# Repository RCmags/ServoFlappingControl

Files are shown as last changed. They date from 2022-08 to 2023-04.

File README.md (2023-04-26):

# Servo controller for an ornithopter :airplane: :bird:
This sketch controls the servos used to power an RC ornithopter (Flapping MAV). Each servo is connected to a wing and flapped independently. 

## How it works
The program is designed to receive 4 PWM inputs from an RC receiver operating in [MODE 2](https://www.rc-airplane-world.com/rc-transmitter-modes.html) and will output 4 PWM signals for off-the-shelf hobby servos. Two servos control the wings and two servos control a V-tail. 

The _aileron (1) and elevator (2)_ channels are used to modify the motion of the wings and to control the tail. The dihedral angle of the wings is altered in unison with the elevator, while the aileron rotates them in opposite directions. Simultaneously, the frequency of the wing-oscillation can be modulated, such that the wings move faster during the downstroke or during the uptroke. Depending on whether this is done symmetrically or assymetrically, one can obtain pitch or roll control. 

<p align="center">
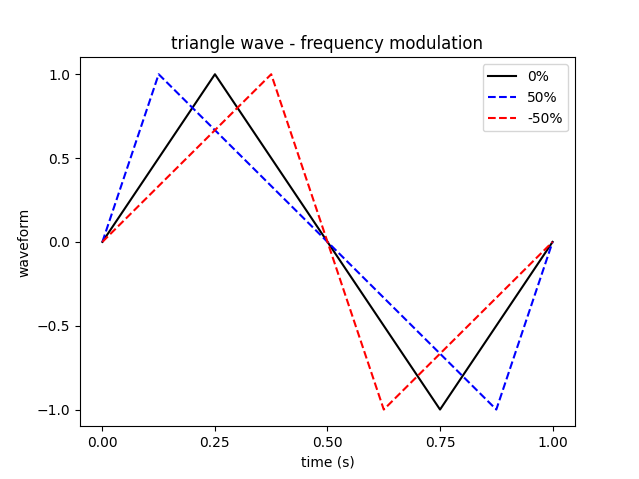
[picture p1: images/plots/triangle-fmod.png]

</p>

The _throttle channel (3)_ controls the amplitude of a fixed-frequency oscillation. By default, the waveform is a triangle-wave, but the throttle can also be used to truncate the wave so it looks more like a square wave. Using a square wave allows the servo to output more mechanical power, but the transition between strokes is very abrupt and stressful. The truncated-wave eases this transition while increasing power compared to a triangle wave.

<p align="center">
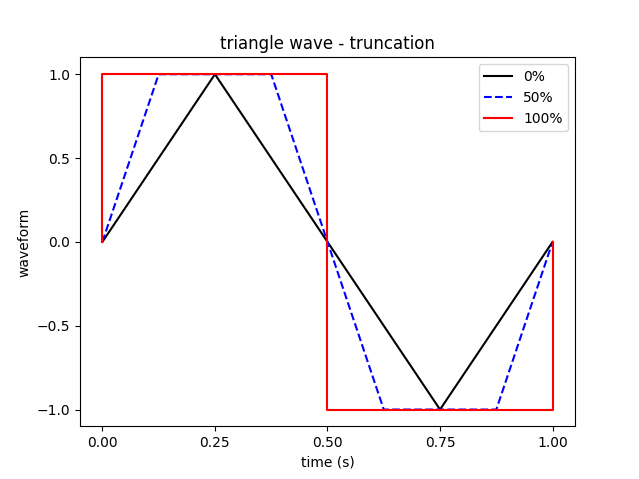
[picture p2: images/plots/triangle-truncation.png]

</p>

The _rudder channel (4)_ is used to assymetrically vary the amplitude of the wings. 

## Schematics
__Nano__: While the program was written for an Arduino Nano, it should be compatible with similar boards. If you don't use tail servos, simply remove them from the circuit and disable their code using the _parameters.h_ file.

<p align="center">
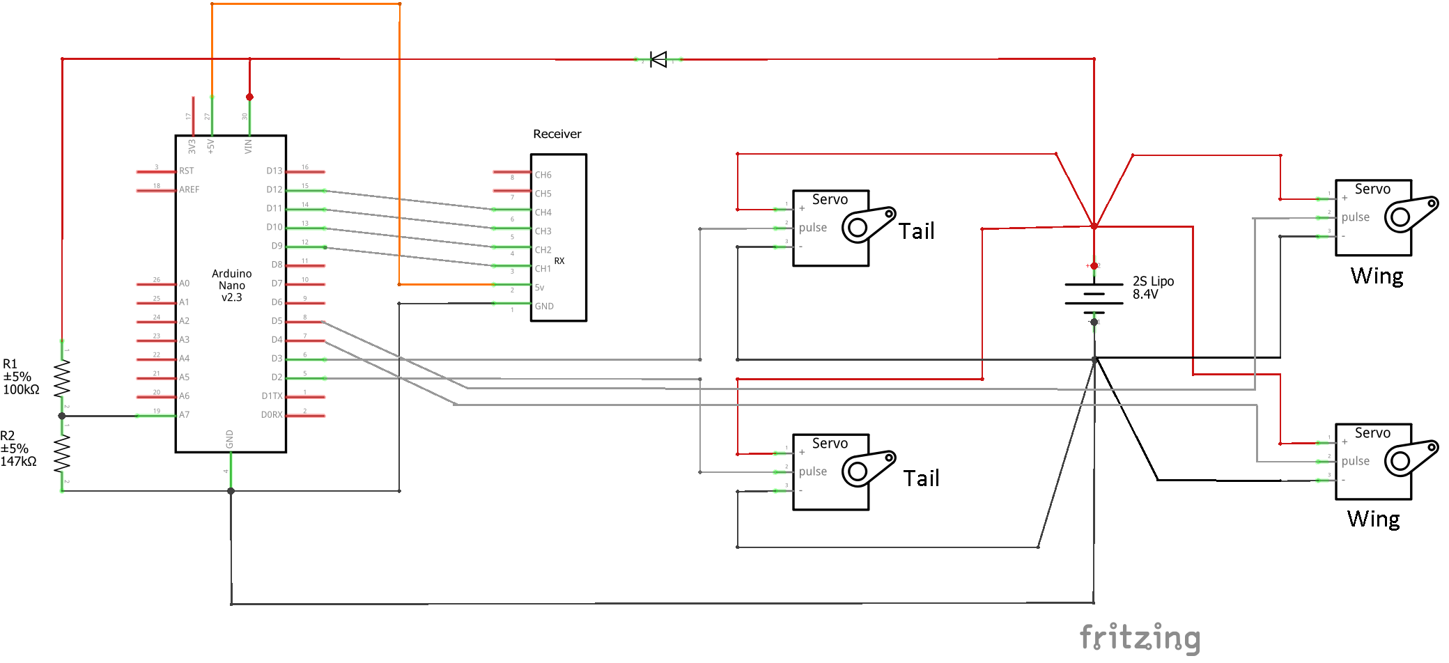
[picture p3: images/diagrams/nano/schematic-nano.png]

</p>

__DigiSpark ATTiny85__: As this microcontroller has fewer pins, it does not support tail servos or a rudder channel. Instead the assymetric amplitude can be mixed into the assymetric dihedral. 

<p align="center">
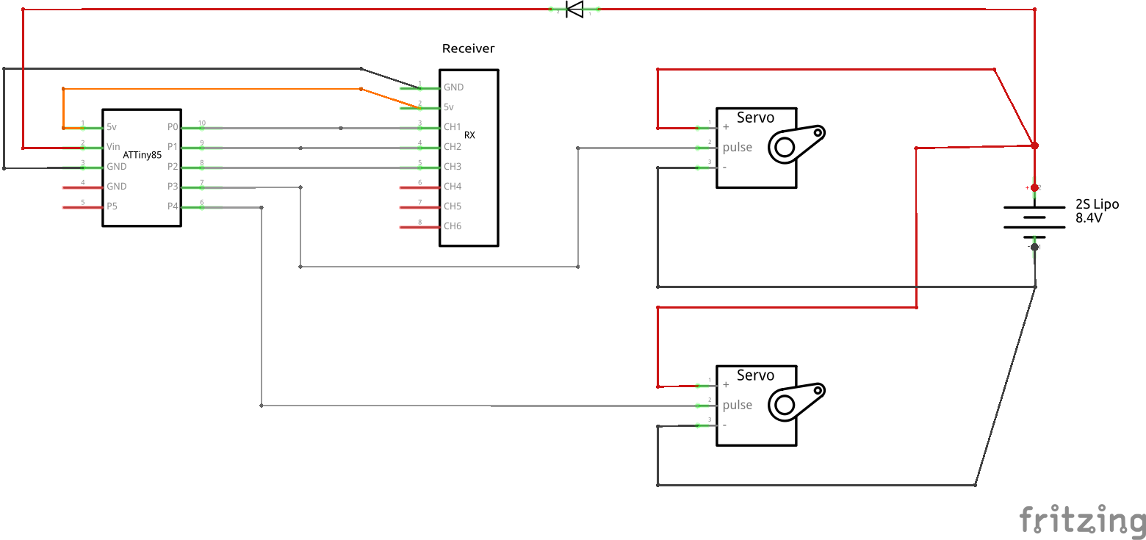
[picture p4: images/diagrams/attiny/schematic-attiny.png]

</p>

## Dependencies
The ATTiny code requires [ATTinyCore](https://github.com/SpenceKonde/ATTinyCore) to compile. 

## Example
See: [explanation and operation of the servo controller](https://youtu.be/T6NfZD_iuEs)

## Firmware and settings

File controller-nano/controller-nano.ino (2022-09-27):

/* ORNITHOPTER SERVO CONTROLLER */

/* Sketch for an arduino NANO that operates the servos of a radio controlled ornithopter. 
 * It commands two servos to flap the wings and (if desired) two servos to control a V-tail.
 * Author: RCmags https://github.com/RCmags
*/

//=============== Connections ================
// See included schematic
  // Inputs:
// Pin 9  -> Receiver CH1
// Pin 10 -> Receiver CH2
// Pin 11 -> Receiver CH3
// Pin 12 -> Receiver CH4
// Pin A7 -> Middle of voltage divider
  // Outputs:
// Pin 2  -> Left  wing servo
// Pin 3  -> Right wing servo 
// Pin 4  -> Left  tail servo 
// Pin 5  -> Right tail servo 

//=================== Code ===================
#include <Servo.h>
#include "parameters.cpp"

//---- global variables 
Servo servo[4]; 
volatile uint16_t pwm_input[4] = {0};

//----- Input signals
// PORTB = {8 .. 13} -> using pins {9 .. 12} = B00011110

/* port change interrupt to read PWM inputs from receiver */
ISR( PCINT0_vect ) {
  static uint32_t initial_time[4] = {0}; 
  static uint8_t port_last = PINB;  
  
  // port changes
  uint32_t current_time = micros(); 
  uint8_t port_rise = ~port_last & PINB;
  uint8_t port_fall = port_last & ~PINB;
  
  // find changing pins
  for( uint8_t index = 0; index < 4; index += 1) {
    uint8_t mask = B00000010 << index;  // Start at PCINT1   
    if( port_rise & mask ) {                
        initial_time[index] = current_time;
    } else if ( port_fall & mask ) {       
        pwm_input[index] = current_time - initial_time[index];
    }
  }
  port_last = PINB;    
}

void setupISR() {
  // enable PORTB interrupts  
  PCICR |= (1 << PCIE0);
  // enable PCINT for pins 9-12                                                   
  PCMSK0 |= (1 << PCINT1);                                              
  PCMSK0 |= (1 << PCINT2);                                              
  PCMSK0 |= (1 << PCINT3); 
  PCMSK0 |= (1 << PCINT4); 
  // set pins inputs
  pinMode(9,  INPUT_PULLUP);
  pinMode(10, INPUT_PULLUP);
  pinMode(11, INPUT_PULLUP);
  pinMode(12, INPUT_PULLUP);
}

//----- Input filter

/* convert PWM inputs to floats and center the readings */
void scaleInputs(float* output) {
  output[0] = float( int16_t( pwm_input[0] ) - PWM_MID );            // roll
  output[1] = float( int16_t( pwm_input[1] ) - PWM_MID );            // pitch
  output[2] = float( int16_t( pwm_input[2] ) - PWM_MIN )*GAIN_THRT;  // throttle
  output[3] = float( int16_t( pwm_input[3] ) - PWM_MID )*GAIN_YAW;   // yaw
}

float positive(float input) {
  return input < 0 ? 0 : input;  
}

//----- Servos

void setupServos() {
    #ifdef USE_TAIL_SERVOS
    pinMode(2, OUTPUT);
    pinMode(3, OUTPUT);
    servo[0].attach(2);
    servo[1].attach(3);
    #endif
    
    /* wing servos */
    pinMode(4, OUTPUT);
    pinMode(5, OUTPUT);
    servo[2].attach(4);
    servo[3].attach(5);
}

//---- Waveform

/* time variable between 0 and 1 */
float floorTime() {
  float t = micros() * 1e-6 * FREQ;
  return t - floor(t); 
}

/* trucanted triangle wave for times between 0 and 0.5 */
float halfWave(float x, float dm) {
  float m = 4 + dm;
  float im = 1.0/m;
  float x1 = 0.25 - im;
  float x2 = 0.25 + im;
  return x < x1 ? 1.0           :
         x < x2 ? -m*(x - 0.25) : -1.0;  
}

/* complete wave for times between 0 and 1 */
float fullWave(float x, float dm) {
  return x < 0.5 ? halfWave(x, dm) : -halfWave(x - 0.5, dm);
}

/* increase and decrease the slope of time */
float freqMod(float t, float ds) {
  constexpr float CONST = 1.0/float(PWM_MAX - PWM_MIN);  
  ds = ds * CONST;
  float m = 1.0/(1 + ds);        
  float im = 0.5/m;
  return t < im ? m*t : (0.5*t - 0.5)/(1 - im) + 1;
}

/* truncated triangle wave with variable ramp-up and ramp-down */
float fwave(float amp, float ds=0) {
  constexpr float CONST = GAIN_WAVE/(PWM_MAX - PWM_MIN); 
  float dm = positive(amp) * CONST;
  float t  = floorTime();
  float tm = freqMod(t, ds);
  return fullWave(tm, dm);
}

//----- Control mixes

/* v-tail mixing with adjustable pitch and roll gain */
void vmix(float* output, float* input, const float gain_x=1, const float gain_y=1) {
  float input_0 = input[0]*gain_x;
  float input_1 = input[1]*gain_y;
  float mix1 = input_1 - input_0;
  float mix2 = input_1 + input_0;
  // return output
  output[0] = mix1;
  output[1] = mix2;
} 

//----- Cutoff

/* low voltage cutoff based on voltage divider */
bool voltageCutoff() {
  constexpr float CONST = (5.0/1024.0)*(RESISTOR_1 + RESISTOR_2)/float(RESISTOR_1);
  static float mean = VOLT_MAX; 
  float volt = analogRead(A7) * CONST;
  mean += (volt - mean)*1e-4;              // average filter n=1e4
  return mean < VOLT_CUT ? HIGH : LOW;     // cutoff voltage
}

//----- Pitching moment correction

/* elevator trim that increases with throttle. Counters pitch-down moment caused by wing flapping */
float pitchTrim(float x) {
  constexpr float M = PITCH_TRIM_Y / float(PITCH_TRIM_X);
  return x < PITCH_TRIM_X ? M*x : PITCH_TRIM_Y;     
}

//----- Main loop

void setup() {
  setupISR();
  setupServos();
  pinMode(A7, INPUT);
}

void loop() {
  float input[4]; scaleInputs(input);

  #ifdef USE_TAIL_SERVOS
  float mix1[2]; vmix(mix1, input, GAIN_ROLL, GAIN_PITCH);
  
  float ptrim = pitchTrim( input[2] );   
  mix1[0] += ptrim;
  mix1[1] += ptrim;

  servo[0].writeMicroseconds( PWM_MID + mix1[0] + TRIM_TLEFT  );    // left tail
  servo[1].writeMicroseconds( PWM_MID - mix1[1] + TRIM_TRIGHT );    // right tail
  #endif
  
  /* wing servos */
  float mix2[2]; vmix(mix2, input, GAIN_ROLL_DH, GAIN_PITCH_DH);   // differential dihedral
  float mix3[2]; vmix(mix3, input,-GAIN_ROLL_FM, GAIN_PITCH_FM);   // frequency modulation
  
  bool cutoff = voltageCutoff();         // dissable flapping at low voltage 
  float amp1 = cutoff ? 0 : positive( input[2] + input[3] );
  float amp2 = cutoff ? 0 : positive( input[2] - input[3] );
  
  float wave1 = fwave( input[2], mix3[0] ); 
  float wave2 = fwave( input[2], mix3[1] ); 
    
  wave1 = wave1*amp1 + mix2[0];          // differential amplitude
  wave2 = wave2*amp2 + mix2[1];
  
  servo[2].writeMicroseconds( PWM_MID + wave1   + TRIM_LEFT   );    // left wing
  servo[3].writeMicroseconds( PWM_MID - wave2   + TRIM_RIGHT  );    // right wing
}

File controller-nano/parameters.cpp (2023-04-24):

/*      CONSTANT     |    VALUE   |  UNIT  |   DESCRIPTION */
/*=========================================================*/
// 1.  Flapping waveform
#define FREQ              3.1     // hz     // Wingbeat frequency [hz]. Use lowest frequency that achieves flight
#define GAIN_WAVE         6.0              /* Triangle wave to square wave gain (truncation). 
                                               A larger gain makes the waveform become more square-like with more throttle */
// 2. Control inputs [negate to reverse direction]
    // I. Base inputs:
#define GAIN_PITCH        1.0               // Tail elevator
#define GAIN_ROLL         1.0               // Tail aileron
#define GAIN_THRT         0.8               // Flapping amplitude. Increases with more throttle
#define GAIN_YAW          0.4               // Differential amplitude. Controlled by rudder
    // II. Differential dihedral:
#define GAIN_PITCH_DH     0.0               // Pitch: symmetric dihedral
#define GAIN_ROLL_DH      0.0               // Roll: asymmetric dihedral
    // III. Frequency modulation:
#define GAIN_PITCH_FM     0.0               // Pitch: wings fall at the same speed
#define GAIN_ROLL_FM      0.0               // Roll: One wing falls faster than the other

// 3. Servo trims 
#define TRIM_LEFT         -80     // us     // left  wing 
#define TRIM_RIGHT        50      // us     // right wing
#define TRIM_TLEFT        0       // us     // left  tail
#define TRIM_TRIGHT       50      // us     // right tail

// 4. Pitching moment correction 
#define PITCH_TRIM_X      250     // us     // Throttle PWM when trim reaches maximum value 
#define PITCH_TRIM_Y      -35  v0    // us     // Maximum pitch trim. Negate to reverse deflection

// 5. Low voltage cutoff [voltage divider]
#define RESISTOR_1        67000   // ohm    // Resistor from ground -> middle 
#define RESISTOR_2        118000  // ohm    // Resistor from middle -> voltage
#define VOLT_CUT          6.0     // volt   // cutoff voltage
#define VOLT_MAX          8.4     // volt   // fully charged voltage 

// 6. Output PWM signal [all servos]
#define PWM_MID           1500    // us     // Center/middle servo position
#define PWM_MIN           1100    // us     // Minimum servo position
#define PWM_MAX           1900    // us     // Maximum servo position

// 7. Other
#define USE_TAIL_SERVOS                     // Comment line to dissable tail servo output (only control wings)

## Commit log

2022-09-22 enable servos
2022-09-23 yaw control
2022-09-24 board name
2023-04-24 add fritzing diagrams
    [schematic-attiny.fzz, schematic-nano.fzz]
